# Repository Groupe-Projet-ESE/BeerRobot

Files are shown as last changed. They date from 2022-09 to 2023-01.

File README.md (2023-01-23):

# <div align="center">BeerRobot</div> 
__Last update of README__ : 23/01/2023

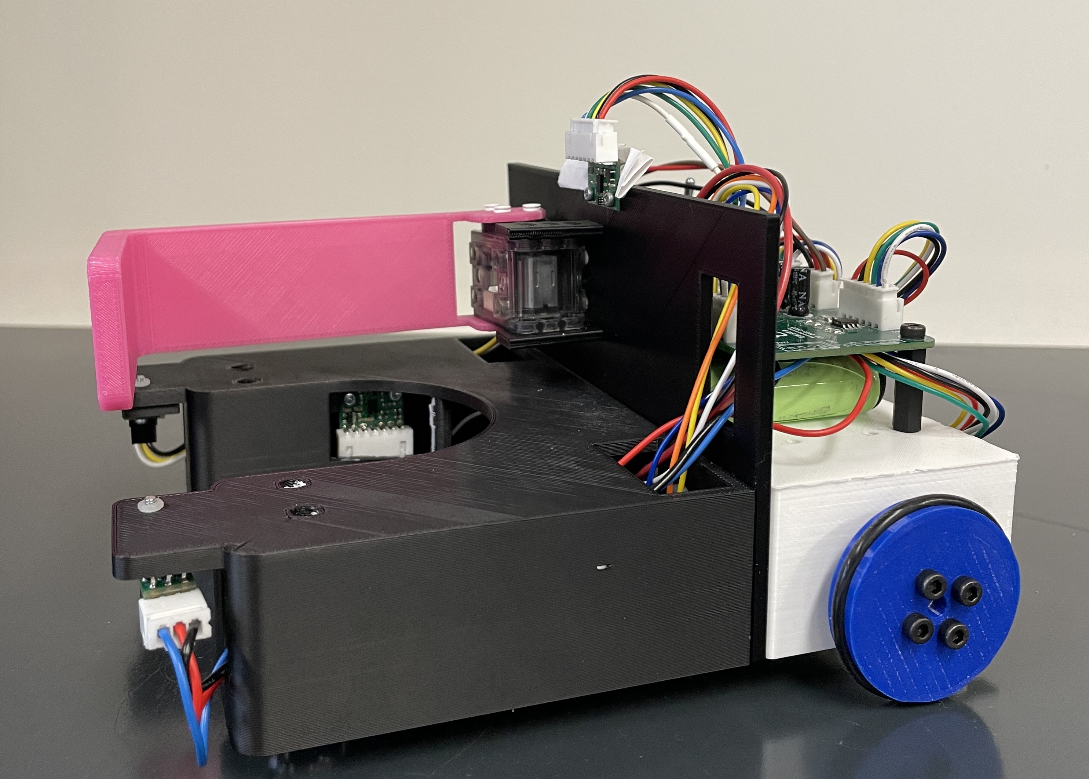
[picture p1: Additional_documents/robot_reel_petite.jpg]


## Introduction
Elèves en option ESE (Electronique et Systèmes Embarqués) au sein de l'ENSEA (Ecole Nationale Supérieures de l'Electronique et de ses Applications), réalisant un robot comme projet central de leur option.  

## Objectifs du projet
Le but du projet est de créer un robot permettant d'attraper des canettes, de relever la couleur de cette dernière, se déplacer avec la canette attrapée et la déposer dans la zone adaptée selon sa couleur. Par ailleurs le robot devra se repérer sur une table afin de ne pas tomber.   

## Matériels et composants à notre disposition

__Microcontroleur__ : STM32G070RBT6 (Farnell : 3365377)  
__Quartz 16 MHz__ : (Farnell : 2853935)  
__Connecteur SWD/STLink__ : (Farnell : 3226055)  
__Driver moteur__ : ZXBM5210-S (Farnell : 3935372)   
__Moteurs__ : DfRobot FIT0520 ou FIT0521   
__Régulateur 5V__ : AZ1117CH2-5.0TRG1 (Farnell : 3942512)  
__Régulateur 3.3V__ : MIC5317-3.3YM5 (Farnell : 2920683)  
__Batterie NIMH 7.2V 1.3Ah__ (RS : 777-0377)    
__Capteur bordure__ : Sharp GP2Y0D805Z0F (Generationrobots : A-000000-00046)   
__Capteur TOF__ : VL53L0X (Generationrobots : A-000000-03233)   
__Capteur de couleur__ : VEML3328 (Farnell : 3517203)  
__Servomoteur__ : XL320 (Generationrobots : A-000000-01282)  
Connecteurs JST 2.54mm  

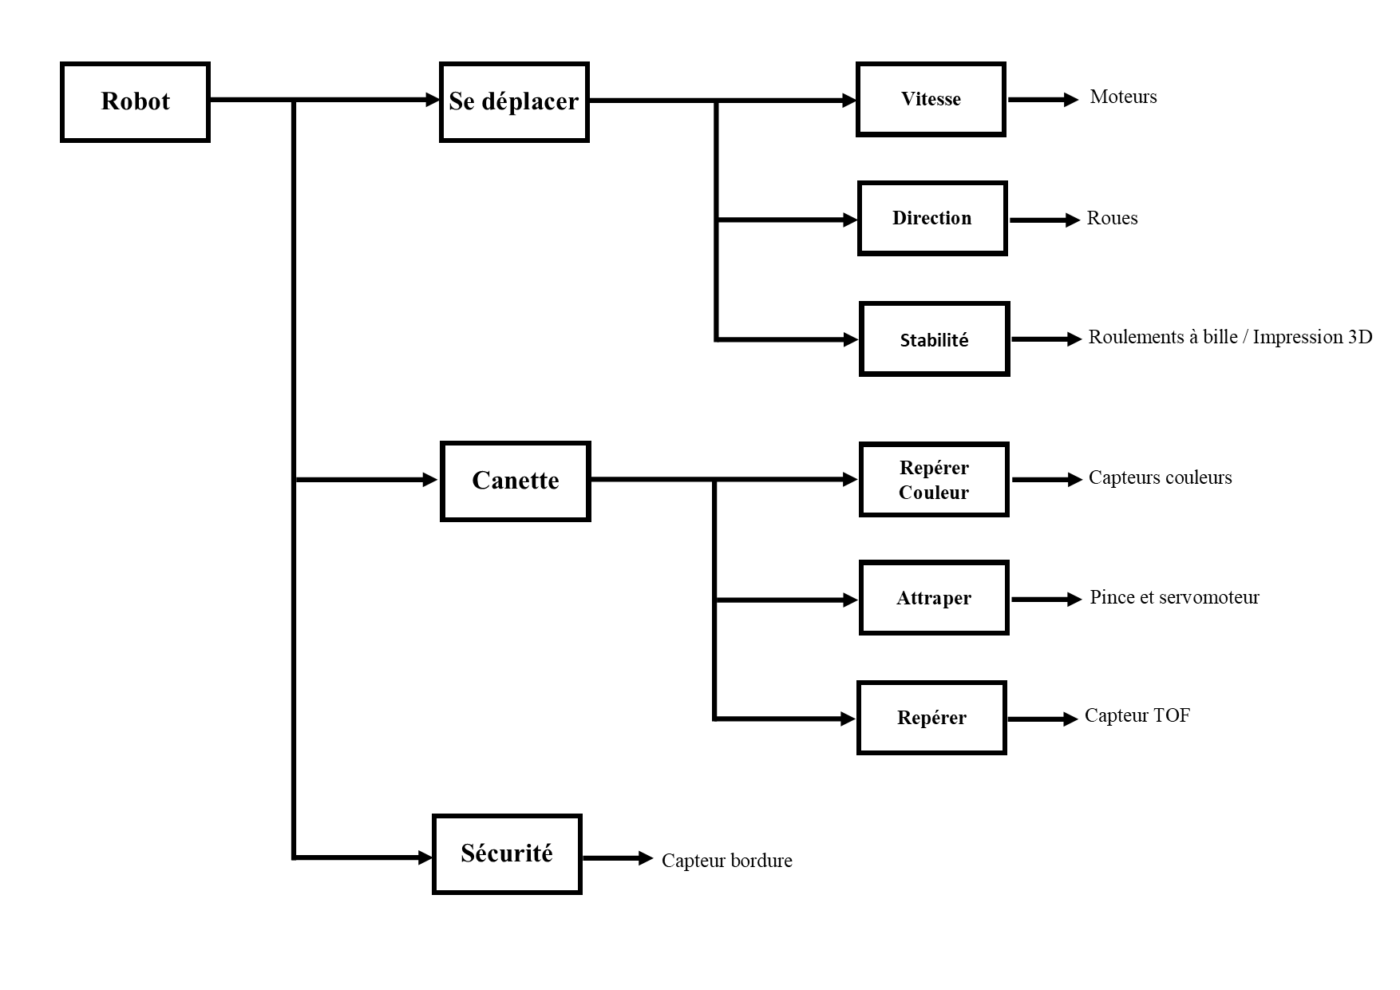
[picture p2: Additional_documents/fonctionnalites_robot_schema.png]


## Membres du groupe et rôles
Le groupe de projet est constitué de 4 membres, chacun ayant divers responsabilités.  
- __Chelsea COMLAN__ : responsable Hardware
- __Loïcia KOEHL__ : responsable intégration
- __Quentin SIMON__ : responsable Software
- __Alix HAVRET__ : responsable livrables

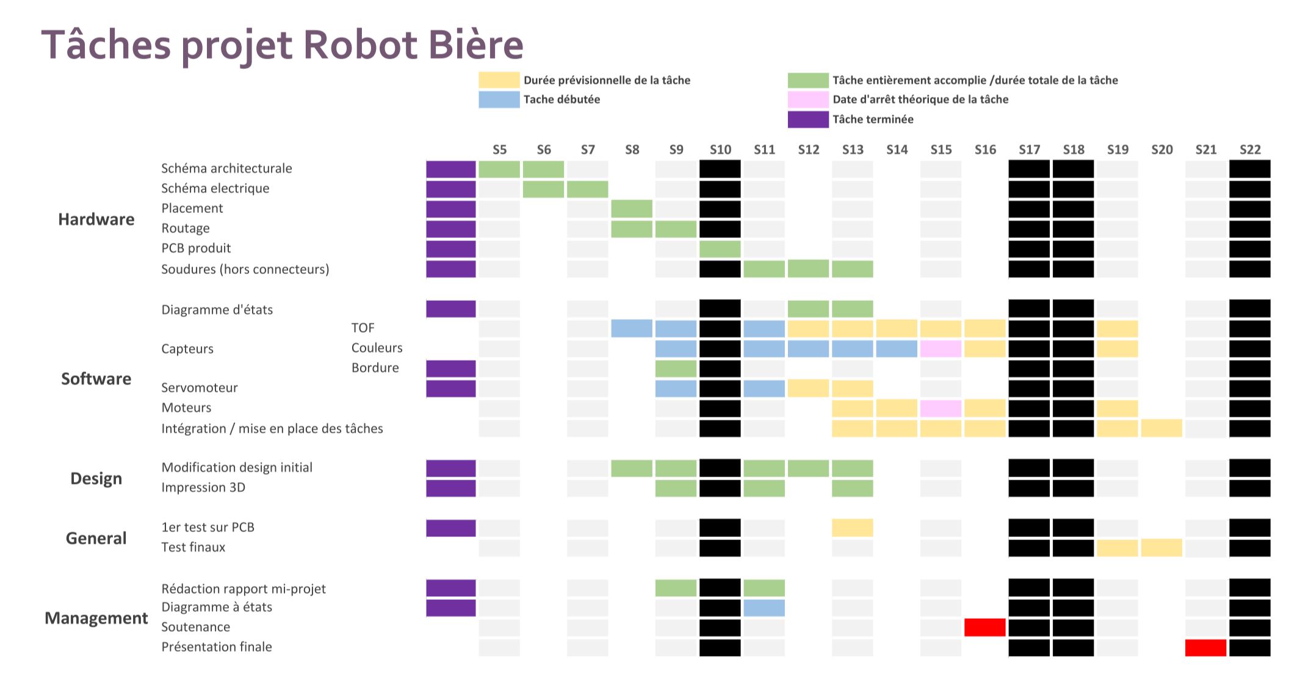
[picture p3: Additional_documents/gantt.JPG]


__Encadrants du projet__ : Mr Fiack , Mr Tauvel  
__Intervenants extérieur__ : Mme Quittel, Mr Jauffrey, Mr Le Bidan  

### Contenus des dossiers
La démonstration finale se trouve sur la master. 

#### Additional documents
Contient l'ensemble des images necessaire à la rédaction de ce README, le rapport de mi-projet rédigé en novembre ainsi que le diaporama de notre présentation du robot en décembre.   

  #### Hardware
Contient le projet Kicad avec l'ensemble des fichiers electronique ainsi que le fichier de routage du PCB.  
Le PCB a été produit à l'extérieur de l'ENSEA.  

  #### Software 
Contient les codes "annexes", c'est à dire les codes des composants testé sur le STM32F746NG.  
Le projet CubeIDE a destination de la STM32G0 (notre microcontroleur de projet) se trouve sur la master. 

  #### 3D 
  Contient certains fichiers 3D pour la réalisation du robot

## Architecture générale du projet

Au debut du projet nous avons eu la liste de l'ensemble des composants auxquels nous avions accès pour la réalisation du robot et afin de remplir ses divers fonctionnalités.   
Le schéma architectural au début du projet nous a permit de définir l'ensemble des entrées necessaires dans notre microcontroleur et les divers flux de données qui allaient entrer en jeu.  
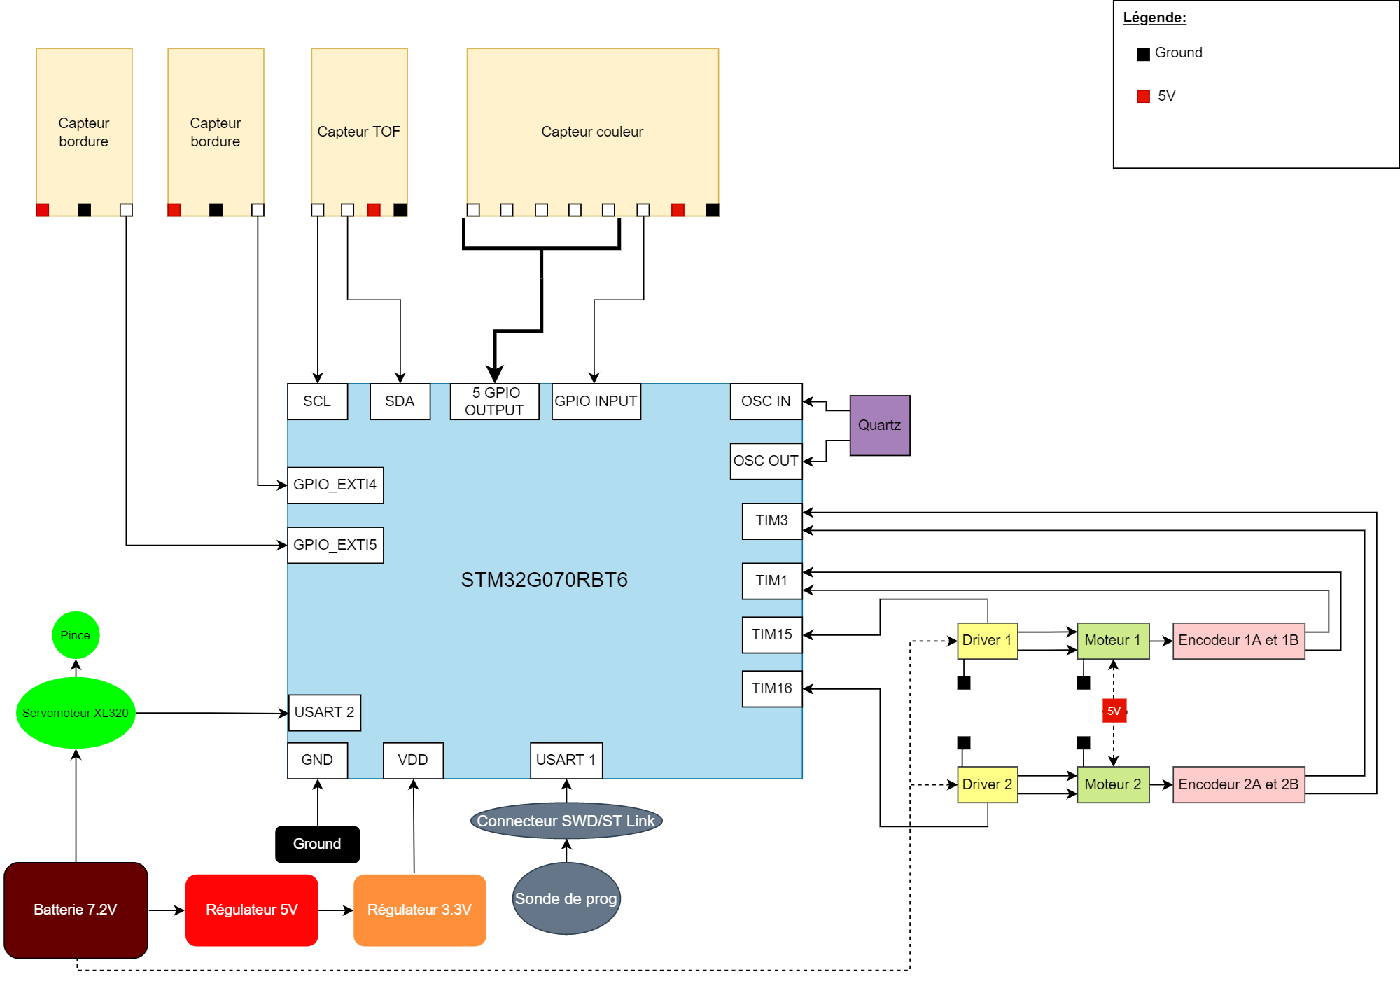
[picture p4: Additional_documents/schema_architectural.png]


### Rôles et utilité des divers composants, capteurs 
#### Moteurs FIT501
Deux Moteurs à courant continu, alimenté en xx V, permettant de faire tourner 2 roues. Le moteur a également un encodeur.  

### Servomoteur XL320
Servomoteur qui permettra de faire bouger la pince necessaire pour saisir les canettes.

### Capteur couleur TCS3200
Capteur permettant de detecter la couleur de la canette à l'aide de filtres superposés à des LEDS.

### Capteur de bordure 
Capteur infra-rouge qui détecte si il y a un object en face de lui.

### Capteur TOF 
Time Of Flight, renvoie le temps qu'a prit la source lumineuse du capteur pour rebondir sur un object et revenir. Cela nous permet d'avoir notre distance par rapport à un objet. (en mm)

## 3D du robot 
Nous avons prit la décision de modifier le design initial du robot sur onshape.  
Ajout d'un roulement en plus à l'avant, modification de l'emplacement de la pince et la forme de celle ci. Une fois le PCB reçu, des modifications ont été effectuées afin de permettre un bon placement de l'ensemble des fils.  
Par ailleurs nous avons aménagés divers emplacements pour les différents capteurs : couleurs, bordure et distance. 

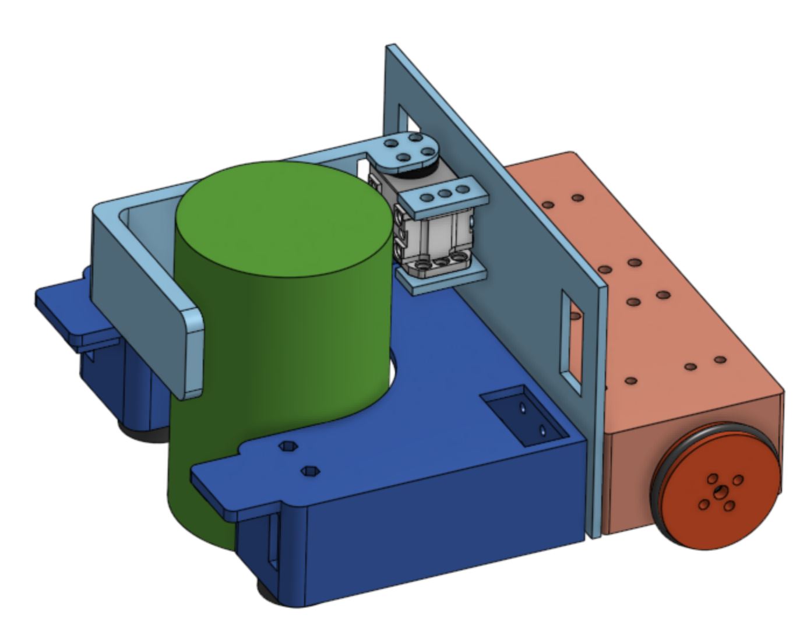
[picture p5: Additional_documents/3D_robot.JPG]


## Hardware 
### Schema electrique
A partir du schema architectural réalisé au début du projet, nous avons commencé le schéma électrique du projet sur Kicad.  
Ce dernier a été séparé en plusieurs feuilles afin de pouvoir organiser les différentes partie : STM32, alimentation, capteurs, moteurs, servomoteur.

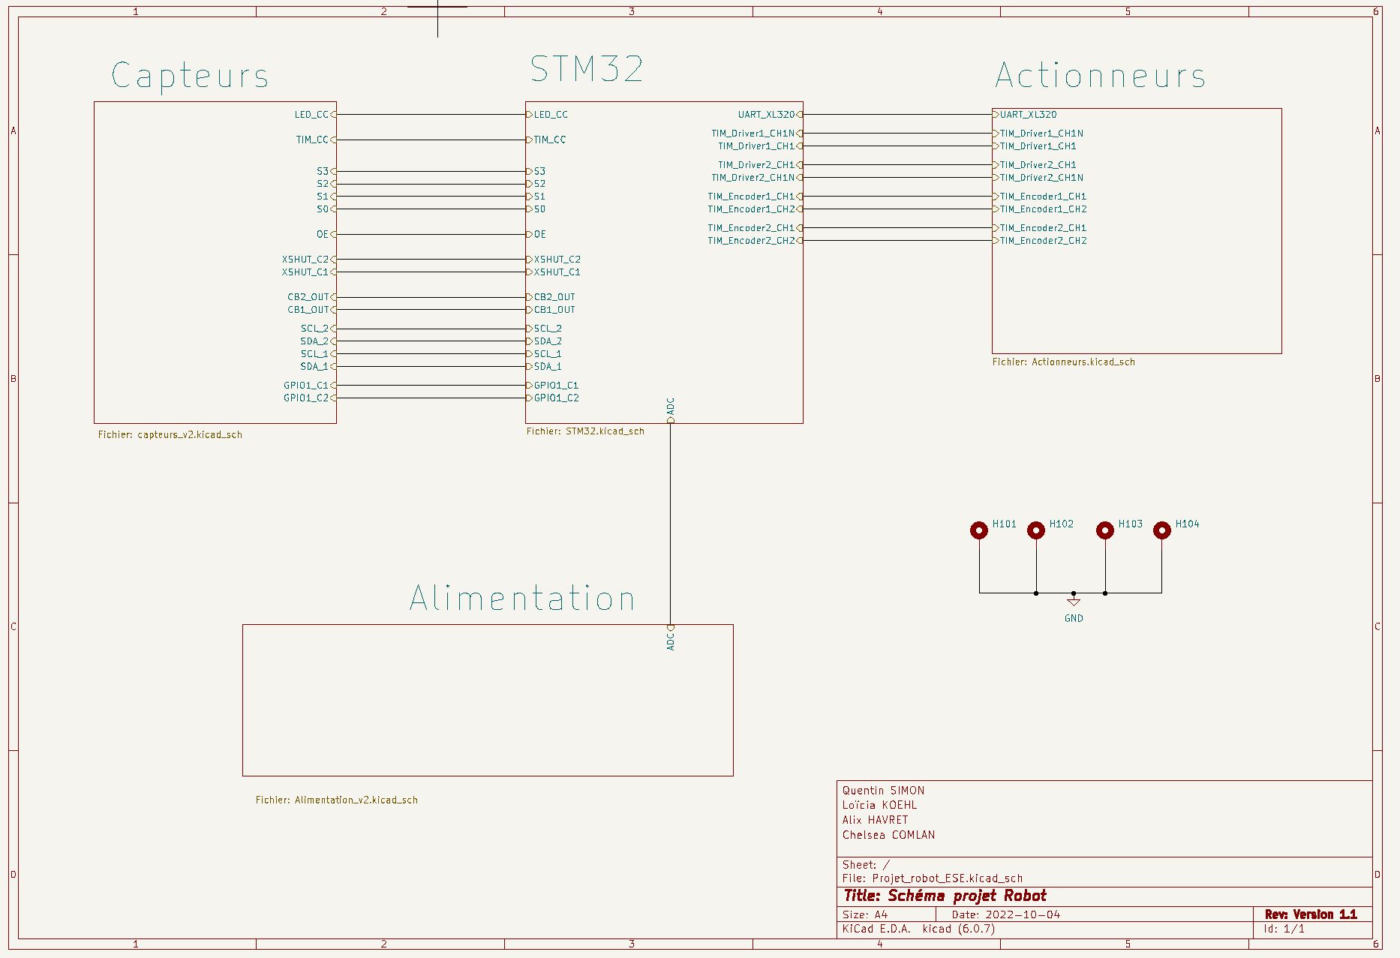
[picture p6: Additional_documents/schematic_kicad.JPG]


### PCB
__09/11/2022__ Reception du PCB  
__Soudeurs__ : Loïcia et Chelsea  
L'ensemble des soudures ont été réalisées à la main, lee 25/11/2022  l'ensemble des composants étaient soudés sur la carte.   
Nous avons soudés les connecteurs au fur et à mesure de la réalisation des tests.

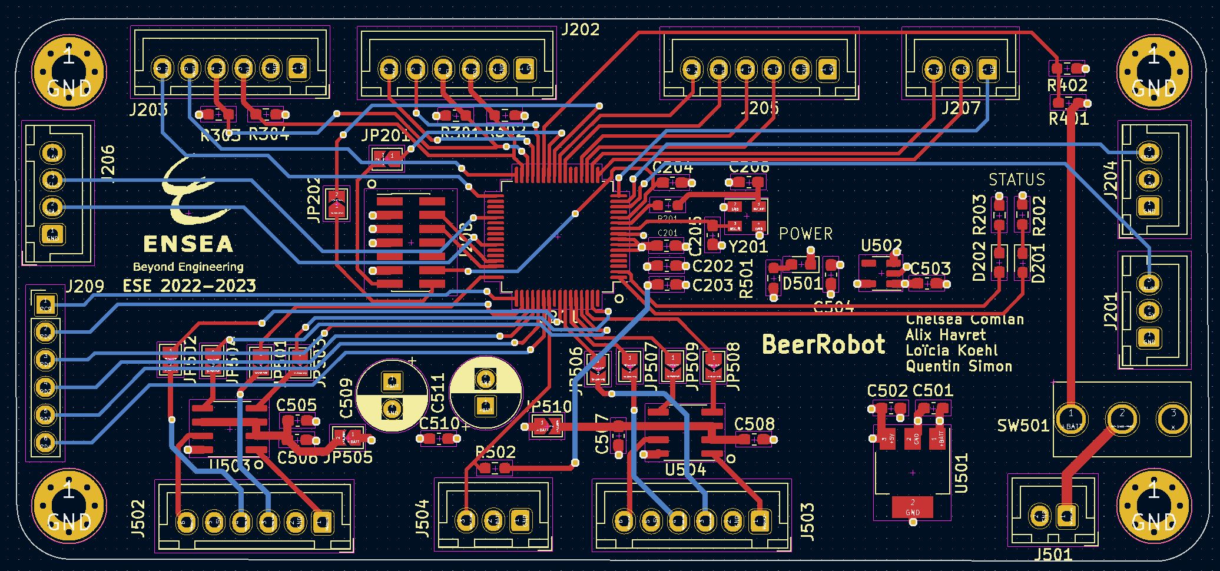
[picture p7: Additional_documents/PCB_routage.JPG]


## Software

Le code sera utilisé dans diverses tâches (utilisation de FreeRTOS). Chaque état décrit dans le diagramme à états correspondra à une tâche.  
Une tâche pourra faire appel à de la donnée, ou en consommer. Dans chaque tâche nous feront appel à divers bouts de code permettant de démarrer un capteur, un moteur, un servo, etc ...  

Pour effectuer nos tests sur les capteurs, nous avons implémentés un shell. Chacun des capteurs ont été validé sur la STM32F746NG, et ensuite leur code était intégré à la STM32G0.
La shell nous a permit de faire une première démonstration. 

### Moteurs : 
Après les premiers tests, nous avons remarqué que pour une même commande vitesse, les 2 roues ne tournaient pas à la même vitesse, de ce fait le robot n'allait pas droit.  Afin de régler ce problème il était nécessaire de mettre en place un asservissement.
#### Asservissement 
Nous avons décidé de faire un correcteur PI (Proportionnel Intégral).  

**schéma**

Pour cela il nous fallait donc récupérer des informations venant du robot et du microcontroleur :  
-	Valeur vitesse demandée  pour les roues
-	Valeur vitesse réelle des 2 roues (les 2 étant différentes du à la qualité des moteurs)  
-	Nombre de tick moteur  

Ces infos nous permettaient alors de créer le correcteur PI avec :  
-	Coefficient proportionnel Kp  
-	Coefficient intégrateur Ki  

Une fois avoir réussi à récupérer la valeur de la vitesse en entrée et le nombre de tick nous avons pu commencer à coder l’asservissement.  

Pour ce faire il fallait que l’on fasse la différence de valeur entre la valeur actuelle et la valeur précédente de vitesse. Par la suite, nous pouvions calculer l’erreur entre la valeur d’entrée et la vitesse du robot pour voir si il avançait à la vitesse souhaitée.  
Une fois toutes la valeurs et calculs mis en place, nous avons pu commencer la recherche des valeurs pour nos coefficients. Il fallait trouver les valeurs avec lesquelles il y avait le moins d’oscillation possible.  

### Fonctionnement des capteurs 
#### Capteur bordure 

#### Capteur TOF 
Le capteur TOF a un driver déja créé, ce qui nous a permit de réutiliser les fonctions déja existantes permettant l'initialisation du capteur, et la récupération des valeurs .L'activation de la pin GPIO nous permet d'acquérir les valeurs en continue tant que le TOF est actif.   
Lorsque que l'on veut utiliser 2 TOF, c'est la pin XSHUT qui rentre en jeux. Les 2 TOF étant sur le même I2C, on activera uniquement le TOF du capteur que l'on veut utiliser.  

#### Capteur couleurs
Non fonctionnel.

__Objectif de la présentation finale :__

La démo implémentée et téléchargée sur la master permet au robot de faire une première phase de démarrage, de se lancer en mode "recherche" canette. Une fois une canette repérée à une certaine distance, le robot continue sa recherche vers la zone où il a capté une canette. Une fois que la canette est captée dans le creue du robot, alors la pince est déclenchée en mode fermeture.

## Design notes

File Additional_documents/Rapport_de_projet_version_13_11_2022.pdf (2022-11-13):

# Rapport de projet de 3

# ème

# année option ESE

# Robot bière

### Encadrants

## - Mr FIACK Laurent - Mr TAUVEL Antoine

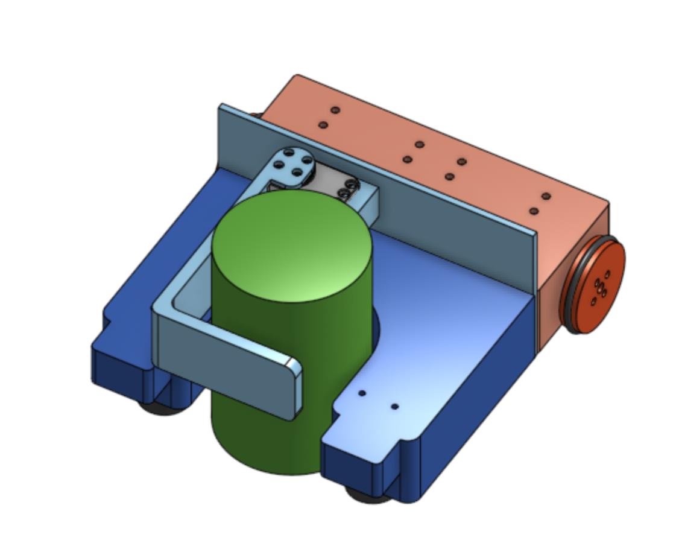
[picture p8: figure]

## COMLAN Chelsea - KOEHL Loïcia - HAVRET Alix - SIMON Quentin

## Novembre 2022

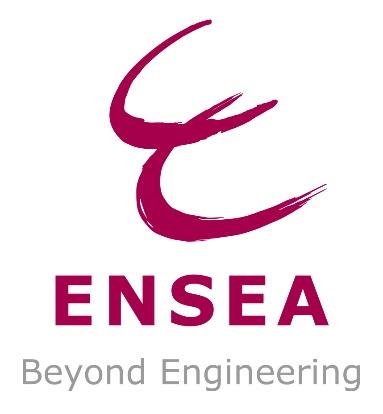
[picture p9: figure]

Rapport de projet | Version du 12/11/2022

1 Introduction_____________________________________________________________________________________3

1.1 Présentation et objectif du défi “Robot Bière"___________________________________________ 3 1.2 Analyse fonctionnelle /CDC_________________________________________________________________ 3 1.3 Organisation du projet ______________________________________________________________________ 4
1.3.1 | GitHub _______________________________________________________________________________________________4
1.3.2 | Equipe _______________________________________________________________________________________________4
1.3.3 | Planning _____________________________________________________________________________________________4
2 Architecture du projet ________________________________________________________________________5

2.1 Ressources ____________________________________________________________________________________ 5 2.1.1 Matérielles___________________________________________________________________________________________5 STM32G070RBT6 _____________________________________________________________________________________________5 2.1.2 Logicielles ___________________________________________________________________________________________5
3 Étapes du développement ____________________________________________________________________6

3.1 Hardware ______________________________________________________________________________________ 6 3.2 CAD _____________________________________________________________________________________________ 6 3.3 Software _______________________________________________________________________________________ 6
3.3.1 | Capteur de bordure _________________________________________________________________________________6
3.3.2 | Capteur couleur VEML3328________________________________________________________________________8
3.3.3 | Capteur couleur SEN0101__________________________________________________________________________9
3.3.4 | Capteur TOF VL53L0X____________________________________________________________________________ 10
3.3.5 | Servomoteur XL320 ______________________________________________________________________________ 11
4 Conclusion _____________________________________________________________________________________14 ANNEXES____________________________________________________________________________________________15

Annexe 1 : schéma architectural _________________________________________________________________15 Annexe 2 : pinout view_____________________________________________________________________________16 Annexe 3 : Schématique capteur couleur 3.3V_________________________________________________16 Annexe 4 : Liste des figures _______________________________________________________________________17

### 1 Introduction

### 1.1 Présentation et objectif du défi “Robot Bière"

Élèves en option ESE (Electronique et Systèmes Embarqués) au sein de l'ENSEA (Ecole Nationale Supérieure de l'Electronique et de ses Applications), réalisant un robot comme projet central de leur option.

Création d'un robot permettant d'attraper des canettes et les déplacer dans des zones, délimitées aux préalables, selon la couleur de la canette.

Le robot devra être capable de :
- Se déplacer
- Saisir une canette
- Se déplacer avec la canette
- Détecter la couleur de la canette
- Ne pas tomber
- Déplacer la canette dans la zone correspondante

### 1.2 Analyse fonctionnelle /CDC

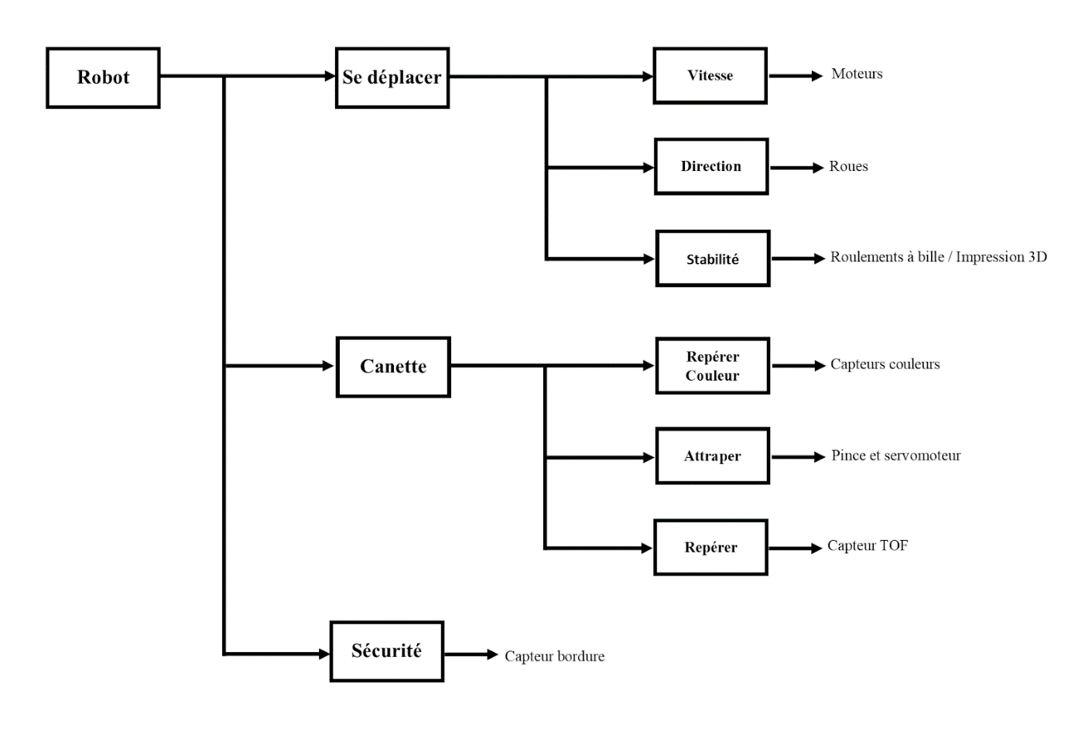
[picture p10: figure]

Figure 1 Analyse fonctionnelle

### 1.3 Organisation du projet

### 1.3.1 GitHub

Github projet (https://github.com/Groupe-Projet-ESE/BeerRobot)

### 1.3.2 Equipe

- Chelsea COMLAN : responsable hardware
- Loïcia KOEHL : responsable intégration
- Quentin SIMON : responsable software
- Alix HAVRET : responsable livrable

### 1.3.3 Planning

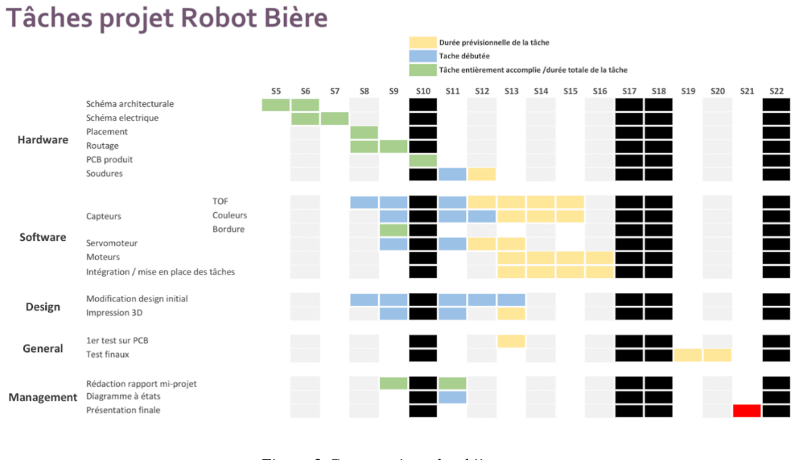
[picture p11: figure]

Figure 2 Gantt projet robot bière

### 2 Architecture du projet

### 2.1 Ressources

### 2.1.1 Matérielles

Nom du composant | Référence
STM32G070RBT6 | Farnell : 3365377
Quartz 16 MHz | Farnell : 2853935
Connecteur SWD/ST Link | Farnell : 3226055
Driver moteur : ZXBM5210-S | Farnell : 3935372
Moteurs FIT 0520 | DfRobot FIT0520
Régulateur 5V AZ1117CH2-5.0TRG1 | Farnell : 3942512
Régulateur 3.3V MIC5317-3.3YM5 | Farnell : 2920683
Batterie NIMH 7.2V 1.3Ah | RS : 777-0377
Capteur bordure | Sharp GP2Y0D805Z0F
Capteur TOF | VL53L0X
Capteur de couleur 5V | SEN0101
Capteur de couleur 3.3V | VEML3328
Servomoteur : XL320 | Generationrobots : A-000000-01282

Connecteurs JST 2.54mm

LED + R/C

Pour notre projet, nous aurons également besoin du matériel de laboratoire : oscilloscope, générateur, multimètre, station de soudures

### 2.1.2 Logicielles

Partie Software
- Cube IDE

PCB
- Kicad pour la réalisation
- JCLPCB pour la production

Design du robot
- On Shape pour la réalisation
- ENSEA pour la production

### 3 Étapes du développement

### 3.1 Hardware

Pour structurer notre carte électronique nous avons dans un premier temps réalisé un schéma architectural (cf Annexe 1)

Ce schéma recense l’ensemble des composants nécessaires au bon fonctionnement de notre robot, ainsi que l’ensemble des ports sollicités.
La visualisation de l’ensemble des ports nécessaires a été faite sur CubeIDE avec le microcontrôleur correspondant (cf Annexe 2).

Sur Kicad nous avons traduit le schéma architectural, avec l’ensemble des composants, et broches nécessaires. Par la suite, le placement et le routage a été réalisé pour être contenu sur un PCB 4 couches de dimensions 11 par 4.

Une fois les PCB reçus, la soudure a débuté.

### 3.2 CAD

En parallèle de la conception du PCB, intéressons-nous à la forme que prendra notre robot. Nous partons du design proposé sur OnShape auquel nous ajoutons ou modifions certaines parties.

Pour assurer la stabilité du robot nous voulons qu’il compte deux roues folles à l’avant, de part et d’autre du creux pouvant accueillir la canette. Pour ce faire, nous devons déplacer le servomoteur qui commande le clapet de la pince afin de placer de manière symétrique les deux roues folles. La pince prend une forme différente, fixée au fond du creux qui accueille la canette.

Afin de placer et fixer les différents capteurs sur le robot, nous créons des ouvertures ainsi que des parois de fixation liées aux dimensions des différents composants comme pour les capteurs TOF qui seront placés à l’avant du robot, le capteur couleur au fond du creux pour la canette et le servomoteur juste au-dessus.

Une fois toutes les pièces modifiées, nous envoyons le design pour impression 3D et attendons que les pièces de notre robot soient fabriquées pour pouvoir l’assembler puis le tester voire l’améliorer.

### 3.3 Software

### 3.3.1 Capteur de bordure

Pour détecter les bordures de la table, on utilise un capteur de bordure Sharp. Ce dernier sera positionné en amont du robot et des roulements à bille, en pointant vers la table.

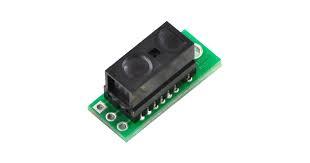
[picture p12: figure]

Figure 3 Capteur de bordure

Il envoie un rayon laser pour détecter si un objet se trouve à une distance inférieure à 5 cm. Si c’est le cas, la sortie est à l’état bas. Sinon, la sortie est à l’état haut.

Le capteur est alimenté avec le régulateur 5V.
Son fonctionnement a été testé avec la carte STM32F746NG.

Ainsi, pour empêcher une chute, on branche la sortie du capteur sur un GPIO en mode EXTI. Puis on active une interruption à chaque front montant.

Putty nous permet d’observer le bon fonctionnement du code.

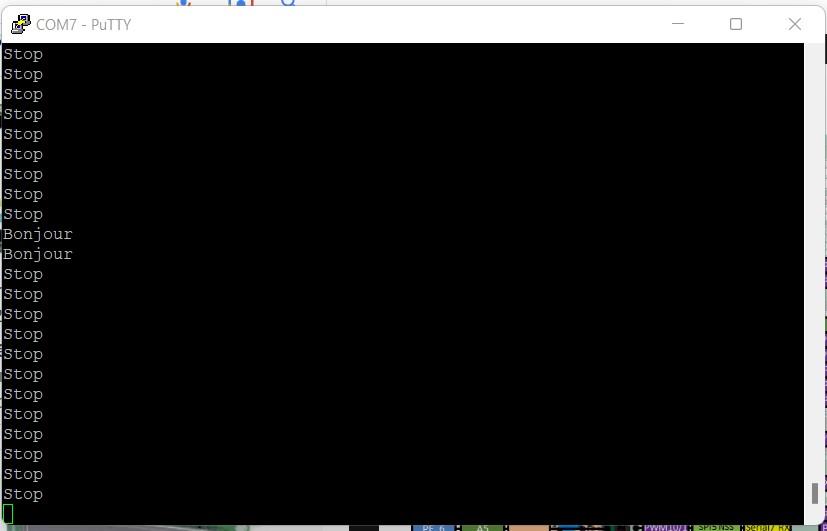
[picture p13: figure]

Figure 4 Sortie de la console TeraTerm pour l'utilisation du capteur de bordure

A terme, le capteur sera placé en amont du robot. Si le vide est détecté, le message d’erreur sera remplacé par une commande d’arrêt moteur, suivi d’une commande de rotation.

On remarque qu’on obtient bien le changement d’état en parallèle à l’oscilloscope.

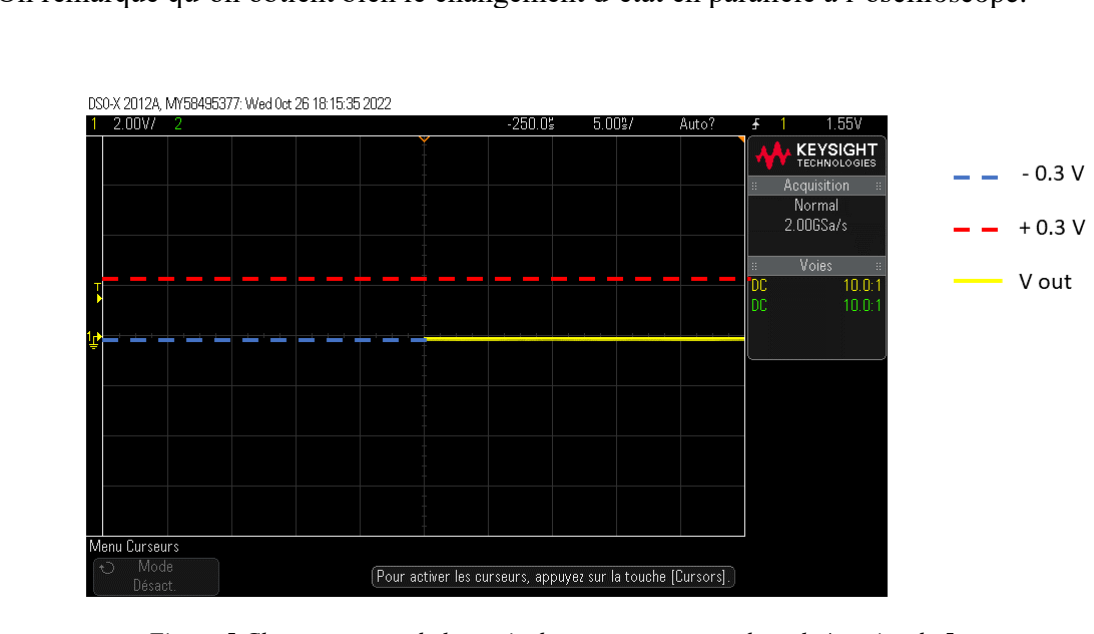
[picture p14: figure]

Figure 5 Chronogramme de la sortie du capteur avec un obstacle à moins de 5 cm

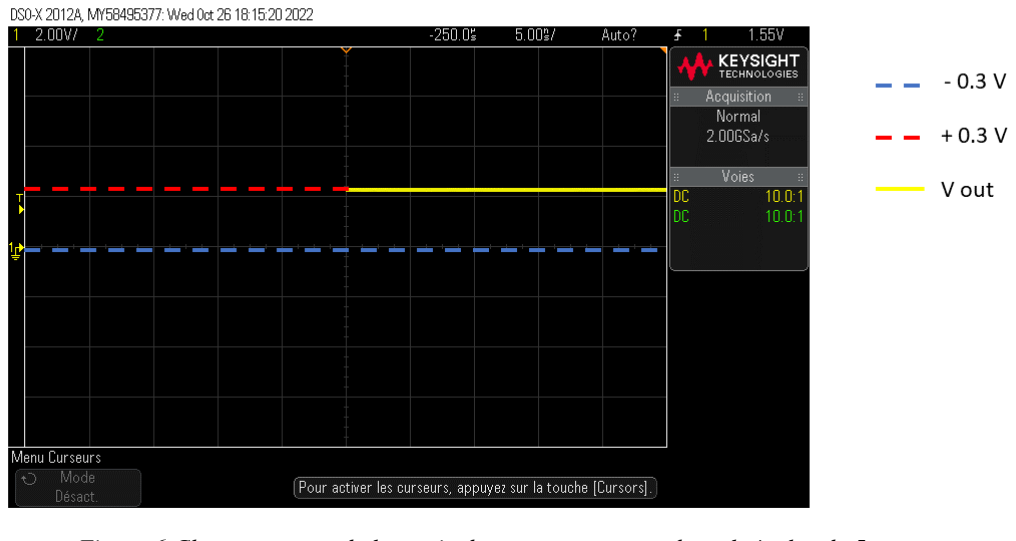
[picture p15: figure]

Figure 6 Chronogramme de la sortie du capteur avec un obstacle à plus de 5cm

### 3.3.2 Capteur couleur VEML3328

Pour détecter la couleur des canettes nous allons utiliser le capteur de couleur VEML3328.

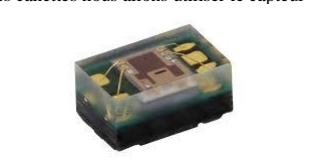
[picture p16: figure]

Figure 7 Capteur couleur VEML3328

Ce capteur mesure la valeur de bleu, rouge, vert et IR d’un objet. Il stocke les valeurs dans des registres sur 16 bits. Le microcontrôleur peut accéder à ces valeurs par liaison I2C, grâce à l’adresse du capteur 0x10 et les codes de commande, 0x05 pour le rouge et 0x06 pour le vert.

Avant toute chose, il faut configurer le capteur grâce au code de commande 0x00.

Cependant, il fonctionne avec une tension d’entrée de 3.3V contrairement à l’autre composant de la carte. C’est pourquoi nous avons réalisé un autre PCB pour le capteur.

Compositions du PCB :

- 4 diodes et 4 résistances pour éclairer la canette
- Un régulateur 3.3V pour alimenter le capteur
- 2 résistances de pull-up pour la communication I2C
- 3 condensateurs de découplage pour le régulateur et le capteur

Cf Annexe 3.

### 3.3.3 Capteur couleur SEN0101

Nous utiliserons un second capteur de couleur. Le SEN0101 de chez DFRobot comprend une puce capteur couleur et 4 LEDs blanches.

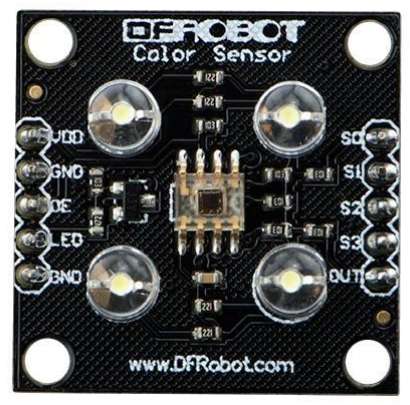
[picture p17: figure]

Figure 8 Capteur couleur SEN0101

Il peut être alimenté en 3.3V ou 5V, on l'alimente par le régulateur 5V. L’utilisation du capteur est testée avec une carte STM32F746NG.

Dans un premier temps, les 4 LEDs blanches sont allumées en mettant à 1 le signal envoyé sur la pin LED du capteur. Le capteur est bien alimenté.

Pour faire fonctionner le capteur, les pins S0, S1, S2, S3 ainsi que le port LED sont branchés sur des ports GPIO_Output. La liaison UART qui passe par le port USB de la carte est elle aussi configurée pour avoir des retours pendant que le code tourne sur la carte afin de débugger. Le but est, à terme, d’afficher la couleur détectée.

Les pins S2 et S3 permettent de choisir le filtre pour détecter une couleur en particulier entre rouge, vert, bleu. Il est également possible de configurer le capteur sans filtre. Les pins 20 et S1 permettent de choisir l’échelle d'intensité lumineuse qui est reliée à la fréquence en sortie du capteur. Dans un premier temps, l’échelle de sortie en fréquence est à 100%.

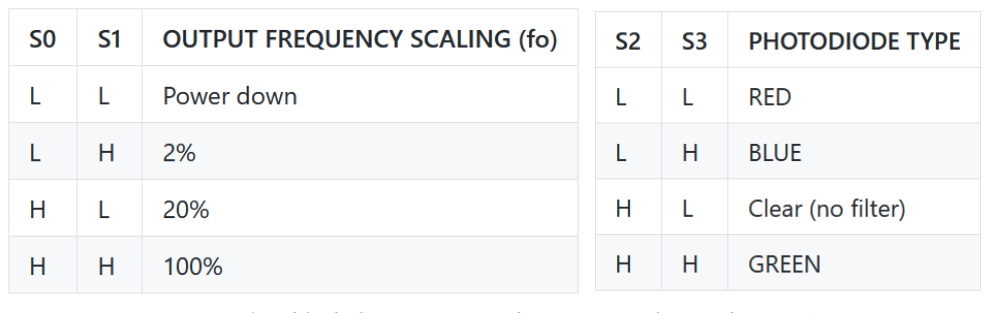
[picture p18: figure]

Figure 9 Table de fonctionnement du capteur couleur et des LEDS

La sortie Out récupère une fréquence qui permet de déterminer la couleur de la canette. La pin Out du capteur est reliée à un timer en mode Input Capture afin de mesurer la fréquence du signal qui sera capté par les photodiodes. Le capteur envoie un signal carré au STM et pour déterminer la fréquence du signal il faut faire la différence entre les temps des fronts montants sur une ou plusieurs périodes.

Mode de fonctionnement des mesures :

Pour lancer la première mesure avec le mode input capture, on utilise HAL_TIM_IC_Start_IT. Selon la configuration choisie, les différentes mesures sont effectuées sur les fronts montants ou descendants ou les deux et les valeurs sont stockées dans le registre IRQ_CCR. Plusieurs mesures permettent de faire une moyenne qui donnera un résultat plus fin de la fréquence et donc de la couleur de la canette. Après avoir effectué
plusieurs | mesures, | il | faut | stopper | les | interruptions | IC | avec | la | fonction
HAL_TIM_IC_Stop_IT.

A chaque interruption, le code appelé est dans la fonction HAL_TIM_IC_CaptureCallback. Le capteur est configuré pour recueillir deux temps de montée consécutifs et en faire la différence pour obtenir la période puis en déduire la fréquence grâce à l’horloge du timer.

A chaque interruption, un compteur est incrémenté pour faire un certain nombre de mesures qui seront moyennées et aussi pour changer le type de filtre. Pour debugger, des printf ont été utilisés dans le code d’interruption ce qui n’est pas recommandé et peut être amélioré. Pour l’heure, des fréquences sont affichées en sortie mais ne semblent pas cohérentes et il reste à moyenner les fréquences et à les faire correspondre aux couleurs pour vérifier la capacité du capteur à différencier et classer les canettes qui seront vertes et rouges.

### 3.3.4 Capteur TOF VL53L0X

Afin de pouvoir repérer les canettes, et la distance du robot vis à vis de ces dernières, nous utilisons un capteur TOF (Time Of Flight). Ce dernier relève la distance en cm (il nous offre une plage de mesure de distance jusqu'à 2 mètres) du capteur par rapport à un objet, quelle que soit sa couleur.

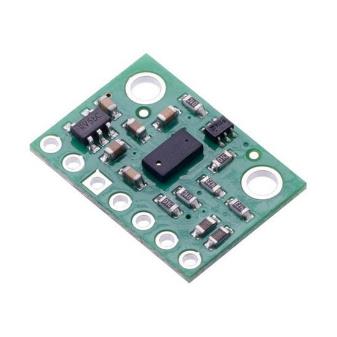
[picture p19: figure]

Figure 10 Capteur TOF VL53L0X

C’est la mesure du temps que met la lumière à revenir au capteur qui permet de déterminer sa distance aux objets

Le VL53L0X de chez STMicroelectronics est incorporé à un module pour rendre son utilisation plus facile d’accès. On utilise la STM32F746NG Discovery pour tester le module.

Le capteur TOF nécessite L’I2C (Inter Integrated Circuit). Le bus I2C permet de faire communiquer entre eux des composants électroniques très divers grâce à trois fils.

- Un signal de donnée : SDA
- Un signal d’horloge : SCL
- Un signal de référence électrique : Masse

Nous alimentons le capteur en 3.3V, et le capteur possède également une broche XSHUT (une entrée) et la broche GPIO1 (une sortie à drain ouvert).

Le VL53L0X possède une librairie (un driver) complète, nécessaire pour pouvoir utiliser les fonctions associées (démarrage, lecture, …).
Le driver une fois téléchargé dans le projet, les fonctions sont simples à utiliser. L’I2C permet d’obtenir des valeurs rapidement, la conversion de ces dernières se fera via des fonctions de la librairie.

Une structure principale contient l’ensemble des éléments nécessaires à la liaison avec l’I2C.

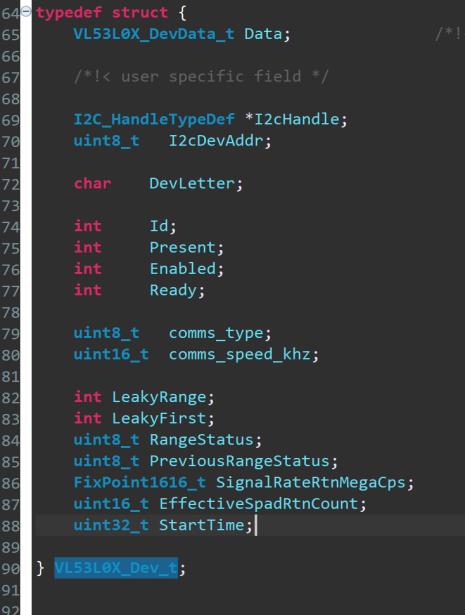
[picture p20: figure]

Figure 11 Structure de la librairie du VL54L0X

Dans notre projet l’objectif est de pouvoir donner la distance entre le robot et une canette, de ce fait une fois que la distance sera égale, ou proche de zéro, les moteurs devront s’arrêter pour que le robot s’arrête et que la pince prenne le relais.

### 3.3.5 Servomoteur XL320

Le servomoteur va nous permettre d’attraper la canette. Dès que le robot va détecter une canette il va avancer vers celle-ci et dès que la distance est bonne, le servomoteur va entrer en action en ouvrant la pince pour que le robot puisse saisir la canette. Nous avons donc commencé par essayer de comprendre comment celui-ci pouvait fonctionner et comment on pouvait le faire tourner.

Figure 12 Servomoteur XL320

Mode de fonctionnement :

Le servomoteur nécessite l’envoie d’une trame. Différents modes sont disponibles, on teste dans un premier temps le mode « write » avec la gestion des LEDS et le mouvement du servomoteur.

Figure 13 Trame write à envoyer au servomoteur

Nous pouvons voir que les données Header, reserved sont fixés, nous n’avons pas à les modifier. Les bits CRC quant à eux sont calculés automatiquement dans le programme. Nous voulons l’utiliser en broadcast donc le packet id est fixé à la valeur donnée dans sa datasheet qui est de 0xFE. L’instruction correspond à ce que nous souhaitons faire. Pour écrire, on utilise la valeur 0x03.

Test LED :

Pour pouvoir allumer la led il faut écrire à l’adresse 0x19 qui correspond à la valeur 25 en décimal.

Figure 14 Commande de la LED

Nous avons testé de contrôler la LED que l’on peut mettre de différentes couleurs :

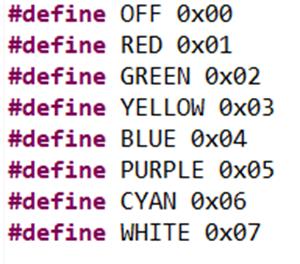
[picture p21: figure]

Figure 15 Commandes couleurs de la LED du servomoteur

Test

On allume la LED et ensuite on l’éteint, donc il nous faut la valeur 0 pour éteindre et 2 pour avoir la LED en vert.

Après l’envoi du code, voici les trames obtenues :

Figure 16 Trame reçue pour le fonctionnement de la LED

Les valeurs obtenues sont celles souhaitées.

Ensuite, nous sommes passé à tester la rotation du servo, pour cela la trame change car l’adresse change, maintenant nous avons l’adresse 0x1E pour le mode Goal Position :

Figure 17 Commande de la rotation du servomoteur

Nous entrons les paramètres souhaités avec la valeur que nous voulons, dans la datasheet nous avons trouvé que le servo-moteur pouvait aller de la position 0 à 1023 et en hexadécimal il faut écrire 0x00 pour la valeur 0 et 0x3FF.

Voici les trames obtenues :

Figure 18 Trame reçue pour la rotation du servomoteur

Si on regarde, nous pouvons voir que les premières données n’ont pas changé, nous changeons les données à partir de la valeur 7 car nous avons 7 valeurs par la suite avec l’instruction qui vaut 3 car on écrit, la valeur 1E correspond au mode que l’on veut donc pour nous la position, le ff 3 correspond à la position que l’on veut.

Dans notre cas nous testons pour la position 1023, juste qu’il faut faire attention car la première valeur correspond au bit de poids faible et les deux dernières valeurs sont calculées par la formule du code qui correspond au bit CRC.

La prochaine étape sera de gérer la vitesse du servomoteur et relier son fonctionnement, et donc l’ouverture de la pince lorsque l’on s’approchera d’une canette.

### 4 Conclusion

En 2 mois nous avons réalisé 90% de la partie hardware. Le PCB est produit, il ne manque que la soudure des composants.
Nous pourrons entamer les premiers tests sur la carte une fois que cette dernière sera prête avec l’ensemble des soudures réalisées.

Tous les capteurs ont un code qui est écrit/en cours d’écriture et testé sur la STM32F746NG Discovery. Les différents capteurs, le servomoteur et les moteurs devront agir ensemble, il nous faudra déterminer les différentes tâches à mettre en place (utilisation de FreeRTOS). Le diagramme d’états, une fois complet, nous permettra de définir les tâches à mettre en place.

Le design du robot a été repensé afin de pouvoir contenir l’ensemble des capteurs, une fois imprimé en 3D, une analyse sera effectuée quant aux emplacements des capteurs et le mode de fonctionnement de la pince, et une phase d’amélioration sera entamée pour obtenir un robot fonctionnel et où tous les capteurs auront un emplacement adapté (selon leur utilisation)

### ANNEXES

Annexe 1 : schéma architectural

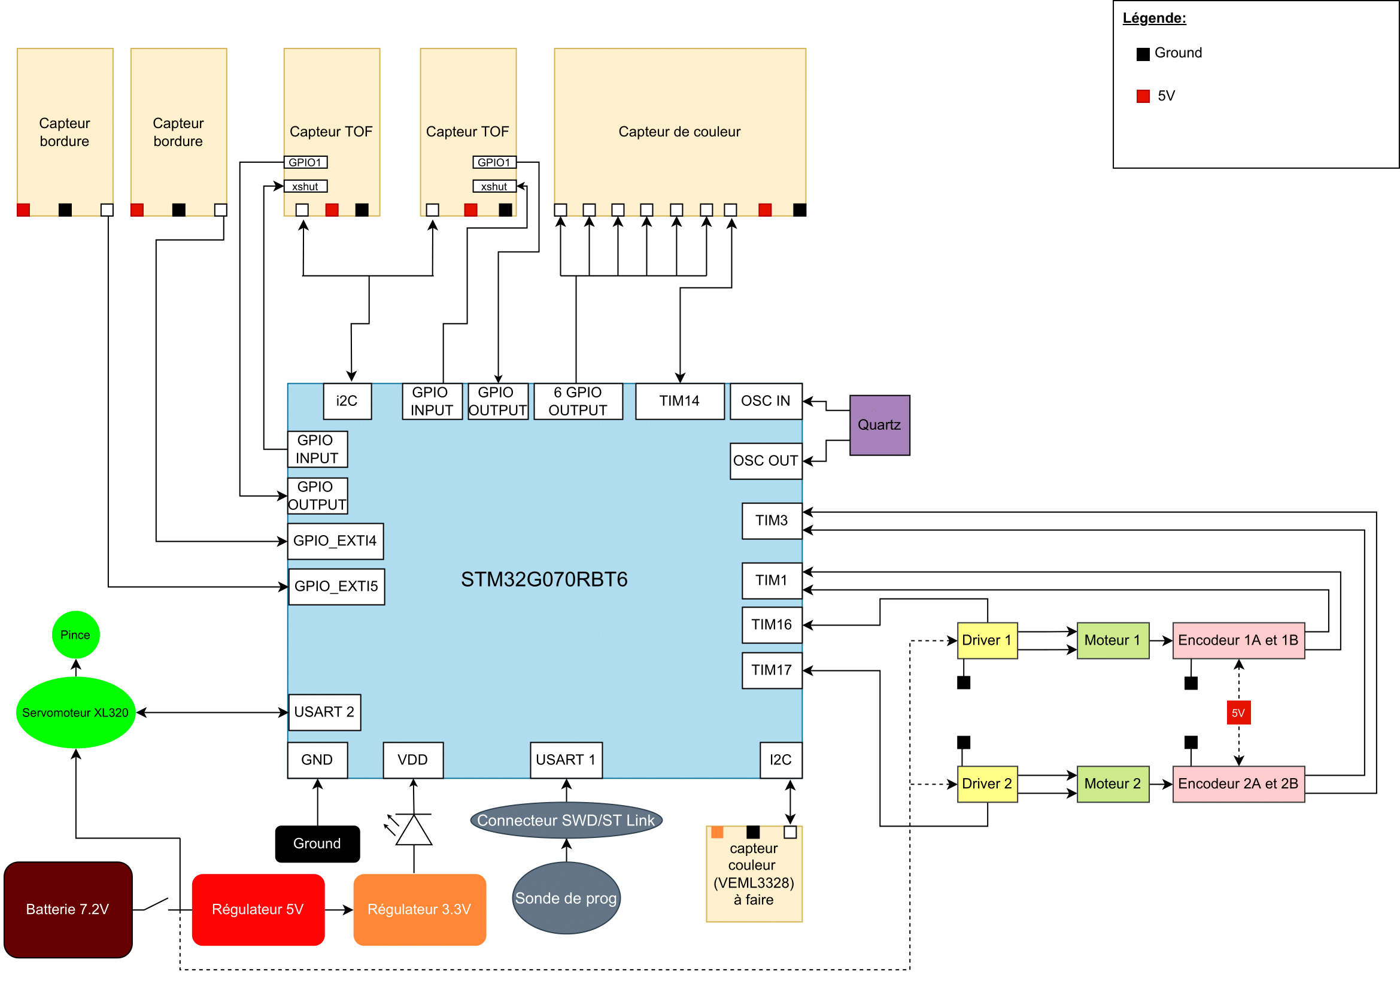
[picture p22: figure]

Figure 19 Schéma architectural

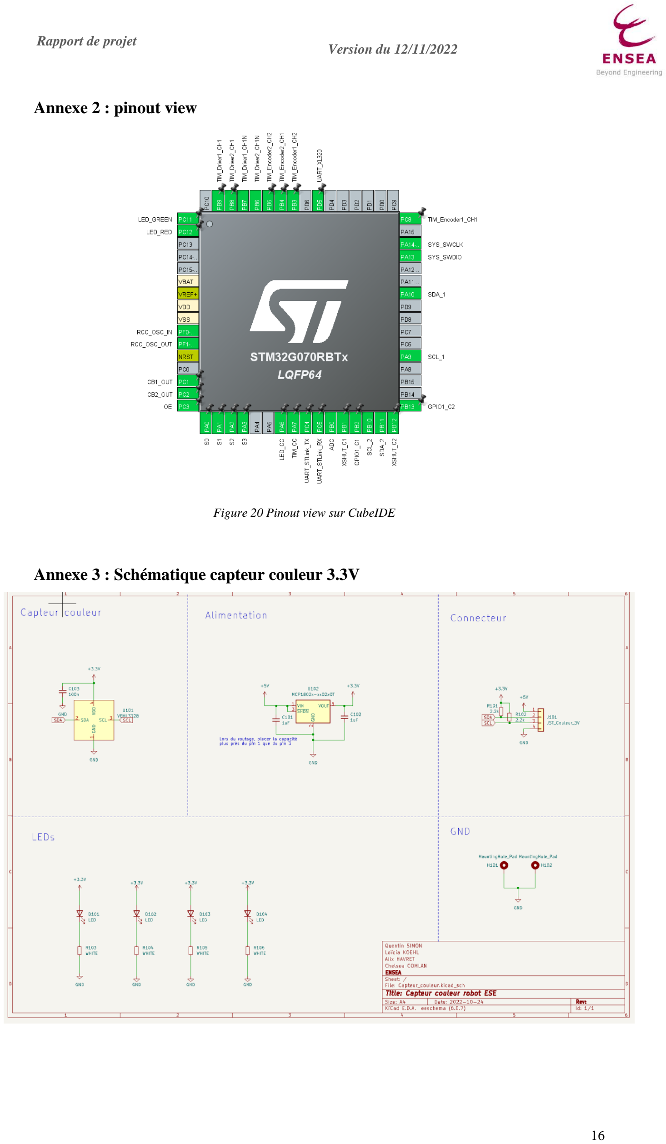
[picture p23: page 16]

Annexe 2 : pinout view

Figure 20 Pinout view sur CubeIDE

Annexe 3 : Schématique capteur couleur 3.3V

Annexe 4 : Liste des figures

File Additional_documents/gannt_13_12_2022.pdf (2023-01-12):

# Tâches projet Robot Bière

S5 | S6 | S7 | S8 | S9 | S10 | S11 | S12 | S13 | S14 | S15 | S16 | S17 | S18 | S19 | S20 | S21 | S22
Schéma architecturale
Schéma electrique
Placement
Routage
PCB produit

Diagramme d'états
TOF
Couleurs
Bordure
Servomoteur
Moteurs

Modification design initial Impression 3D

1er test sur PCB
Test finaux

Rédaction rapport mi-projet Diagramme à états
Soutenance
Présentation finale

Tâche entièrement accomplie /durée totale de la tâche Date d'arrêt théorique de la tâche
Tâche terminée

### Design

### General

### Management

### Hardware

### Software

Capteurs

Intégration / mise en place des tâches

Soudures (hors connecteurs)

Durée prévisionnelle de la tâche Tache débutée

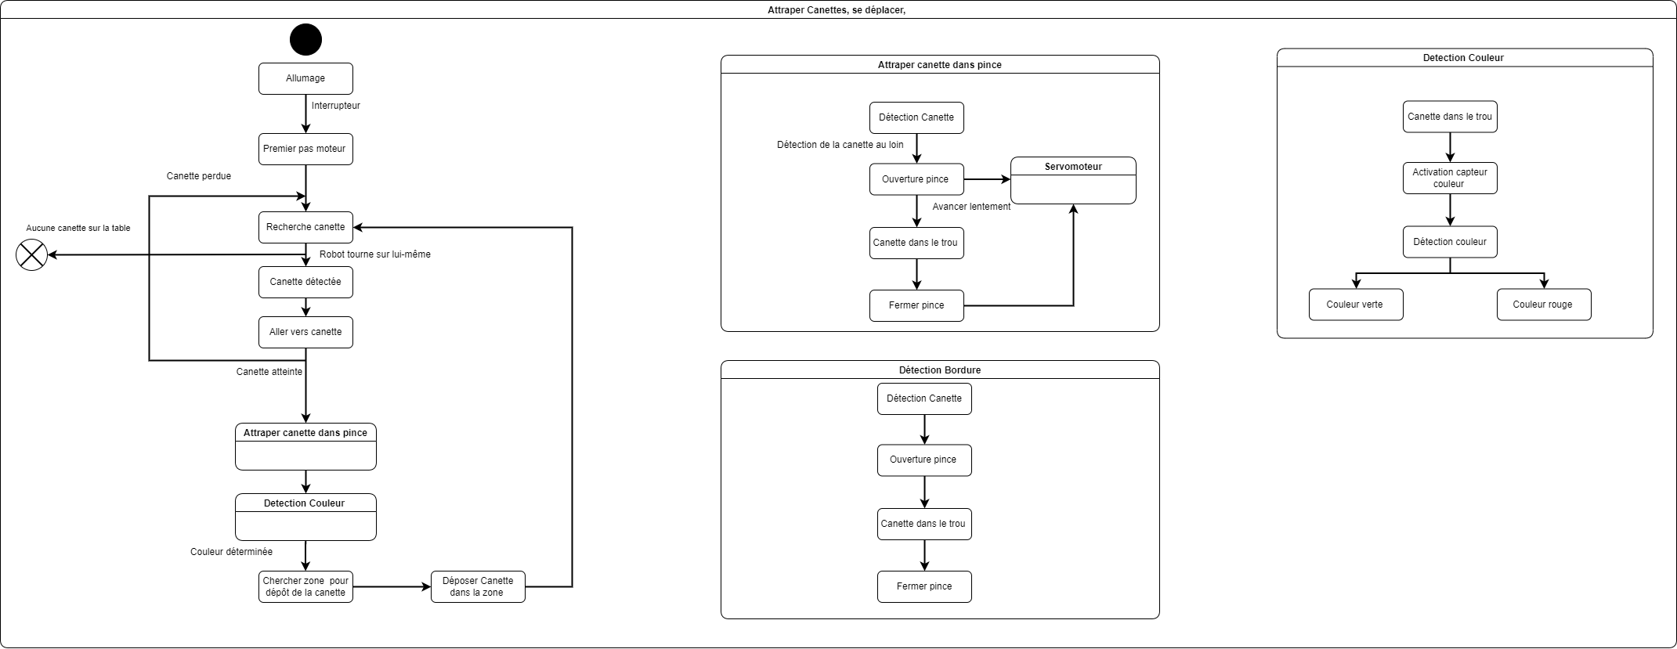
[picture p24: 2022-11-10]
Additional_documents/diagramme_d_etats.png

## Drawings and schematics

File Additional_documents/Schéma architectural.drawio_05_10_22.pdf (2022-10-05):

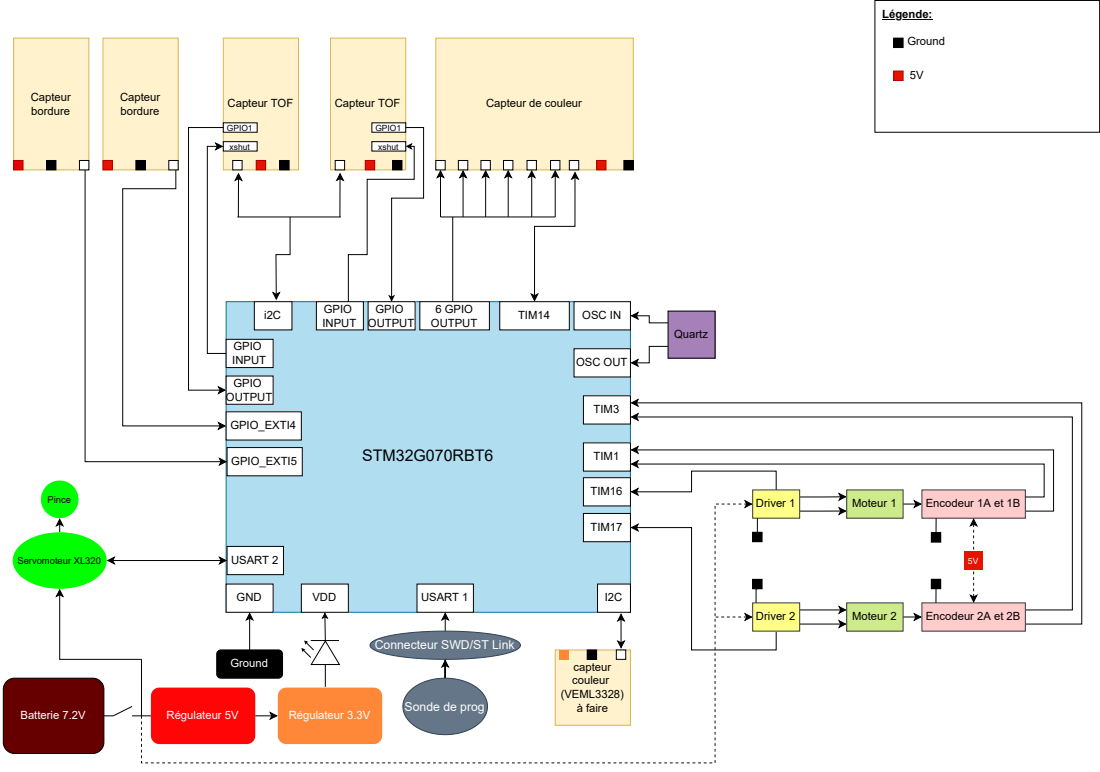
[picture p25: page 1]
Capteur TOF; Capteur de couleur Capteur; bordure; STM32G070RBT6; TIM1; GND; OSC IN; OSC OUT; USART 1; USART 2; TIM3; VDD; Quartz; Capteur bordure; GPIO_EXTI5; GPIO_EXTI4; Batterie 7.2V; Driver 1; Régulateur 5V; Driver 2; Régulateur 3.3V; Moteur 1; Moteur 2; Ground; 6 GPIO; OUTPUT; TIM14; Encodeur 1A et 1B; Légende:; Encodeur 2A et 2B; Servomoteur XL320; Pince; TIM16; TIM17; xshut; GPIO INPUT; GPIO1; GPIO OUTPUT; capteur couleur (VEML3328) à faire

Connecteur SWD/ST Link

Sonde de prog

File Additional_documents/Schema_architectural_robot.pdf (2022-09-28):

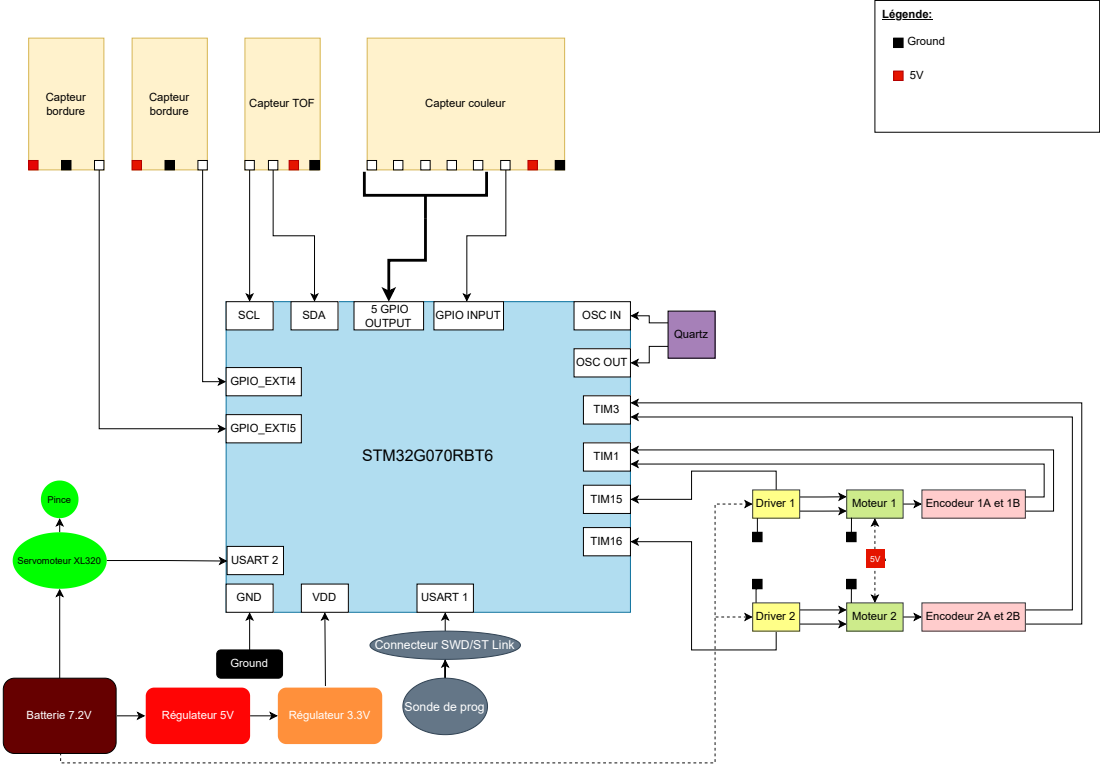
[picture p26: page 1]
Capteur TOF; Capteur couleur Capteur; bordure; STM32G070RBT6; SCL; SDA; TIM1; GND; OSC IN; OSC OUT; USART 1; USART 2; TIM3; VDD; Quartz; Capteur bordure; GPIO_EXTI5; GPIO_EXTI4; Batterie 7.2V; Driver 1; Régulateur 5V; Driver 2; Régulateur 3.3V; Moteur 1; Moteur 2; Ground; 5 GPIO; OUTPUT; GPIO INPUT; Encodeur 1A et 1B; Légende:; Encodeur 2A et 2B; Servomoteur XL320; Pince; TIM15; TIM16

Connecteur SWD/ST Link

Sonde de prog

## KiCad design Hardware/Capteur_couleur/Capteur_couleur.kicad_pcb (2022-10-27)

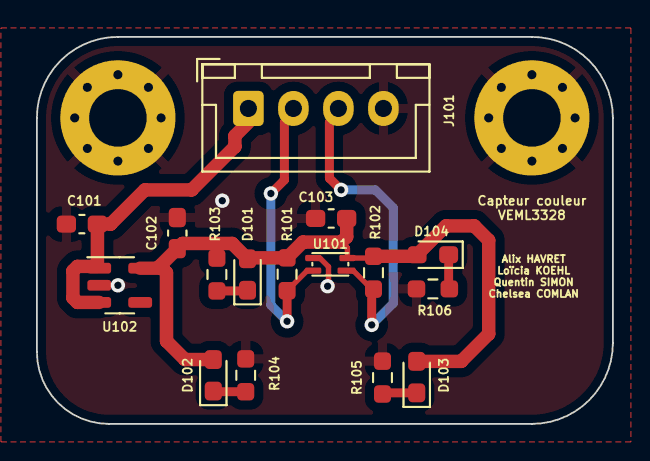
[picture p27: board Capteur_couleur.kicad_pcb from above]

Board: 2 copper layers, 32.0 x 21.5 mm, 18 parts (0 on the bottom side), 9 nets.

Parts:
C101, C102: 1uF; C_0603_1608Metric_Pad1.08x0.95mm_HandSolder
C103: 100n; C_0603_1608Metric_Pad1.08x0.95mm_HandSolder
D101, D102, D103, D104: LED; LED_0603_1608Metric_Pad1.05x0.95mm_HandSolder
H101, H102: MountingHole_Pad; MountingHole_3.2mm_M3_Pad_Via
J101: JST_Couleur_3V; JST_XH_B4B-XH-A_1x04_P2.50mm_Vertical
R101, R102: 2.2k; R_0603_1608Metric_Pad0.98x0.95mm_HandSolder
R103, R104, R105, R106: WHITE; R_0603_1608Metric_Pad0.98x0.95mm_HandSolder
U101: VEML3328
U102: MCP1802x-xx02xOT; SOT-23-5

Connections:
+3.3V: C102.1, C103.1, D101.2 (A), D102.2 (A), D103.2 (A), D104.2 (A), R101.1, R102.1, R103.2, U101.4 (VDD), U102.5 (VOUT)
+5V: C101.1, J101.1, U102.1 (VIN), U102.3 (~SHDN)
GND: C101.2, C102.2, C103.2, H101.1, H102.1, J101.4, R104.2, R105.2, R106.2, U101.1 (GND), U102.2 (GND)
unnamed: D101.1 (K), R103.1
unnamed: D102.1 (K), R104.1
unnamed: D103.1 (K), R105.1
unnamed: D104.1 (K), R106.1
SCL: J101.3, R102.2, U101.3 (SCL)
SDA: J101.2, R101.2, U101.2 (SDA)

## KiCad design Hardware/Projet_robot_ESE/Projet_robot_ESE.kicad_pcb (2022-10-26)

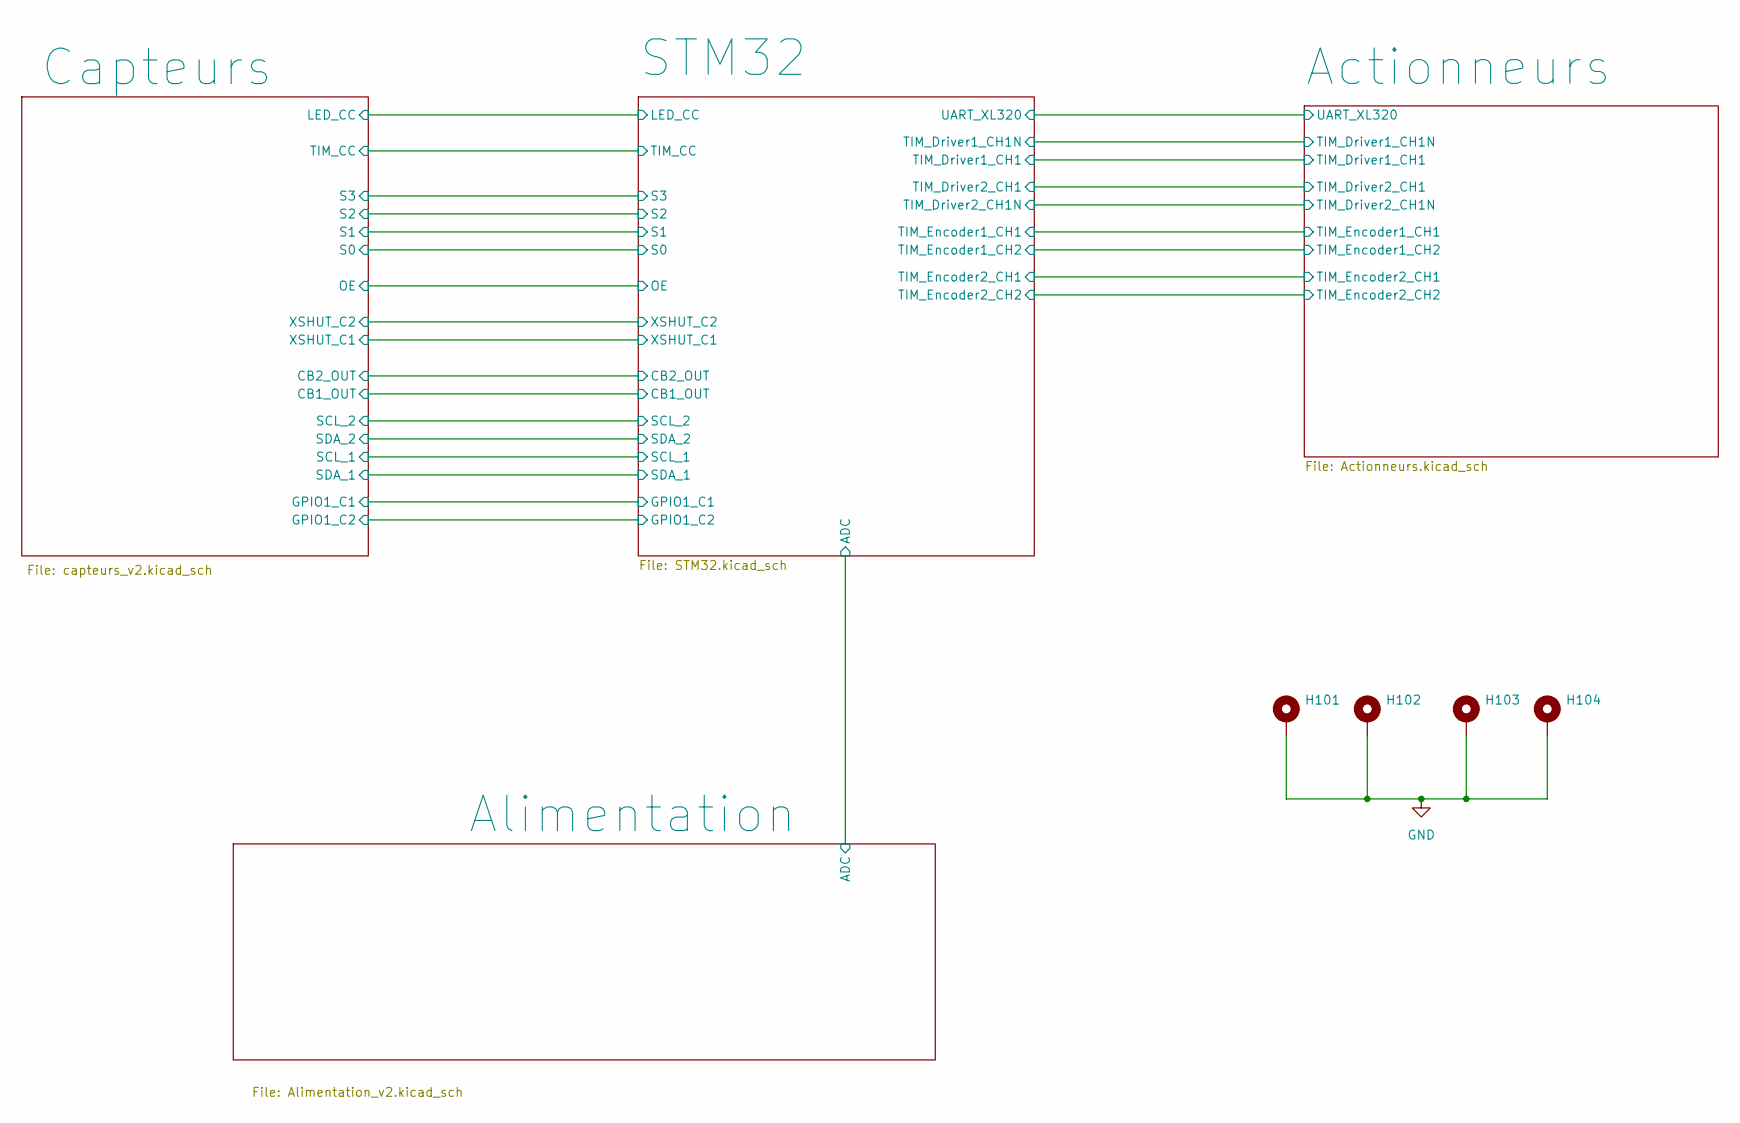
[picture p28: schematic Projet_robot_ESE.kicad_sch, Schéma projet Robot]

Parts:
H101, H102, H103, H104: MountingHole_Pad; MountingHole_3.2mm_M3_Pad_Via

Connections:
GND: H101.1, H102.1, H103.1, H104.1; also elsewhere on the board

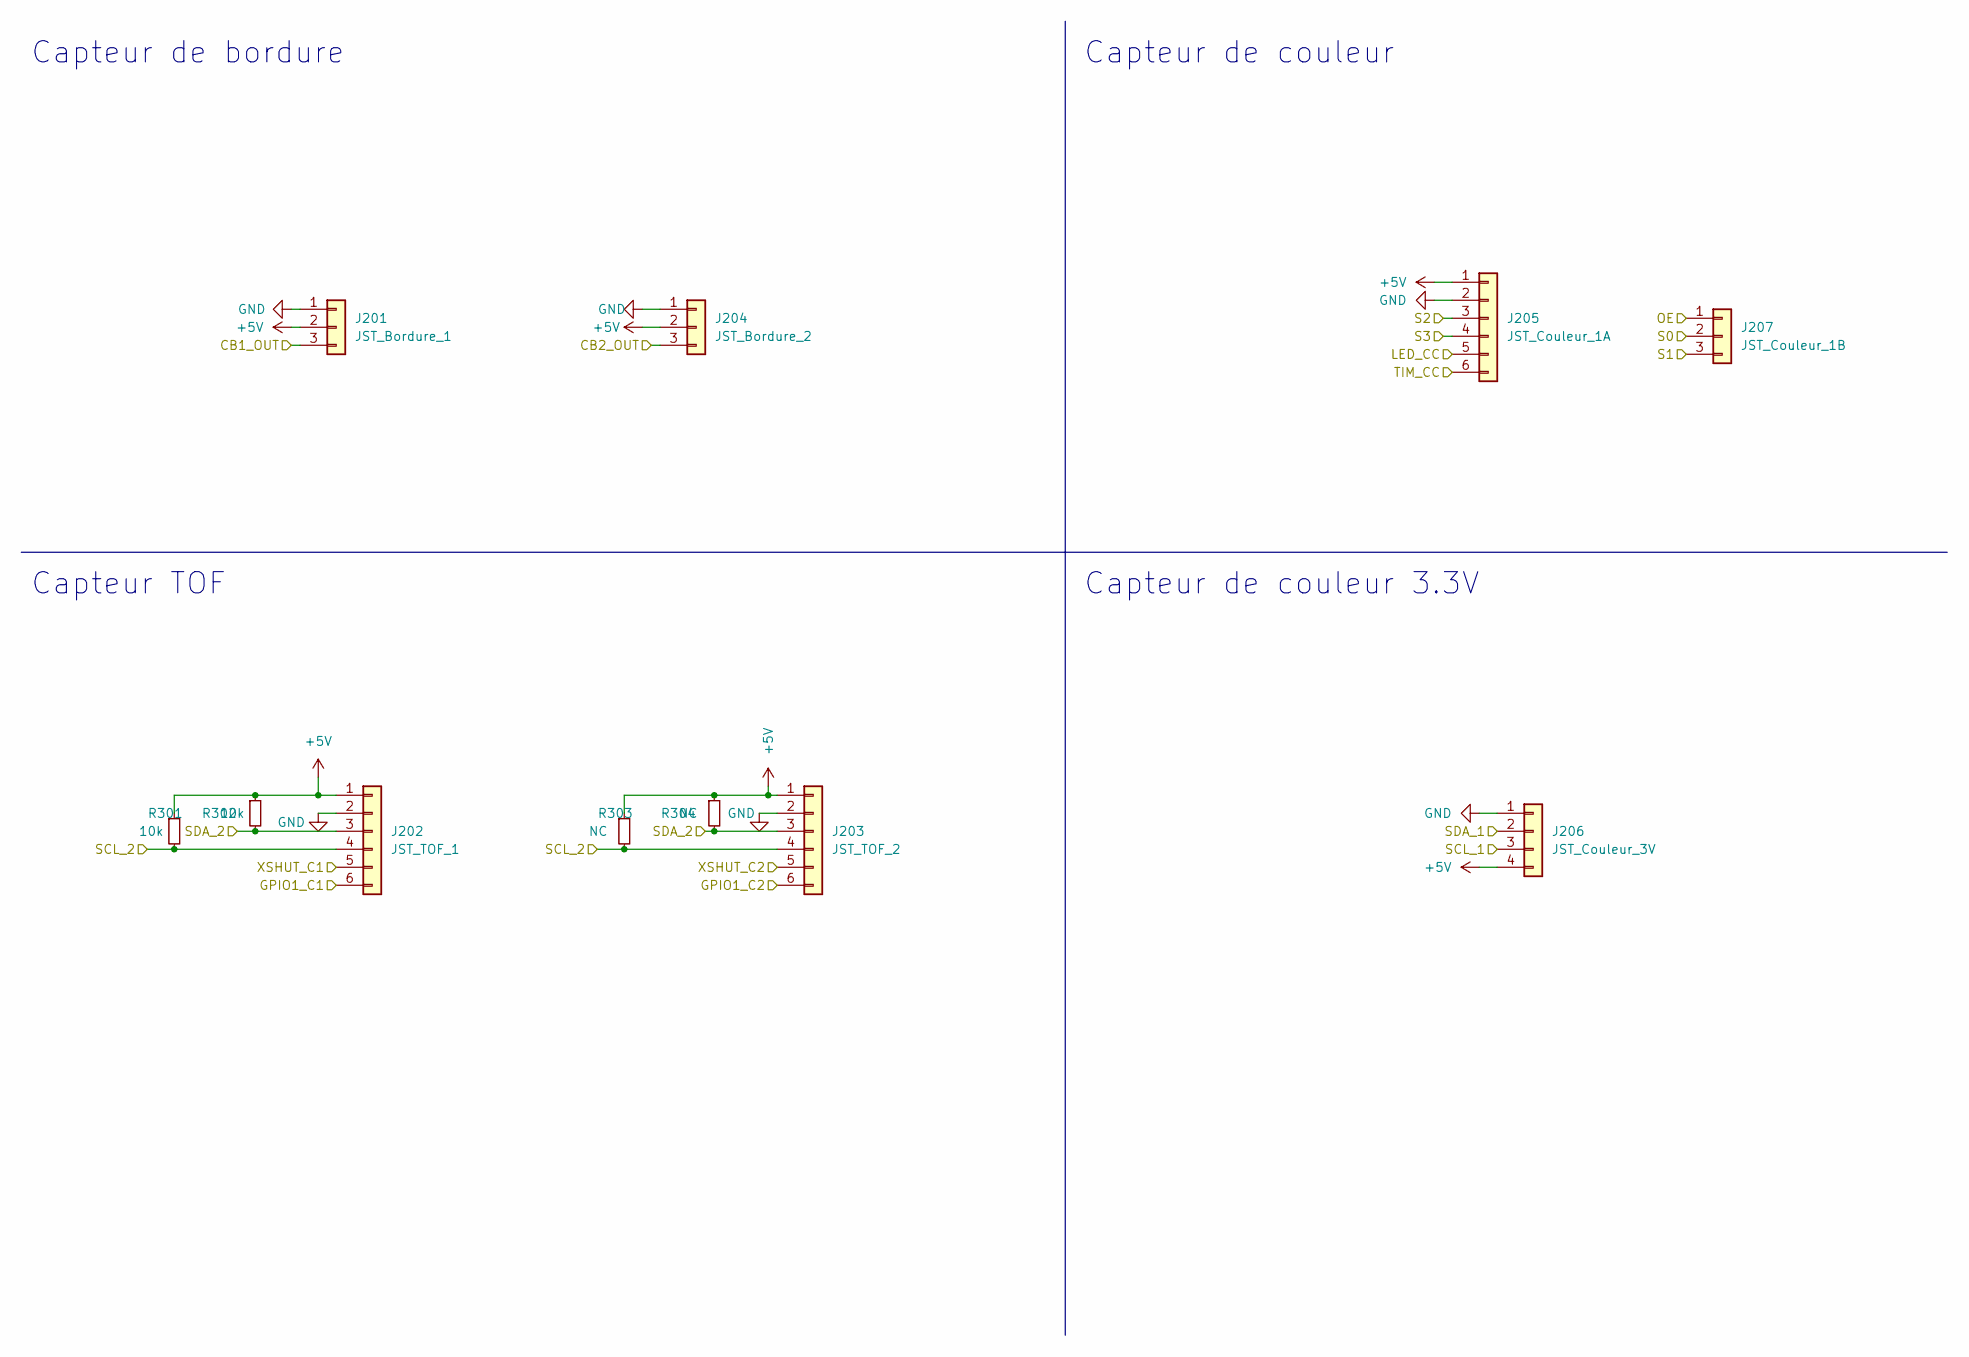
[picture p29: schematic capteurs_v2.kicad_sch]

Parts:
J201: JST_Bordure_1; JST_XH_B3B-XH-A_1x03_P2.50mm_Vertical
J202: JST_TOF_1; JST_XH_B6B-XH-A_1x06_P2.50mm_Vertical
J203: JST_TOF_2; JST_XH_B6B-XH-A_1x06_P2.50mm_Vertical
J204: JST_Bordure_2; JST_XH_B3B-XH-A_1x03_P2.50mm_Vertical
J205: JST_Couleur_1A; JST_XH_B6B-XH-A_1x06_P2.50mm_Vertical
J206: JST_Couleur_3V; JST_XH_B4B-XH-A_1x04_P2.50mm_Vertical
J207: JST_Couleur_1B; JST_XH_B3B-XH-A_1x03_P2.50mm_Vertical
R301, R302: 10k; R_0603_1608Metric_Pad0.98x0.95mm_HandSolder
R303, R304: NC; R_0603_1608Metric_Pad0.98x0.95mm_HandSolder

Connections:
+5V: J201.2, J202.1, J203.1, J204.2, J205.1, J206.4, R301.1, R302.1, R303.1, R304.1; also elsewhere on the board
/Capteurs/CB1_OUT: J201.3; also elsewhere on the board
/Capteurs/CB2_OUT: J204.3; also elsewhere on the board
/Capteurs/GPIO1_C1: J202.6; also elsewhere on the board
/Capteurs/GPIO1_C2: J203.6; also elsewhere on the board
/Capteurs/LED_CC: J205.5; also elsewhere on the board
/Capteurs/OE: J207.1; also elsewhere on the board
/Capteurs/S0: J207.2; also elsewhere on the board
/Capteurs/S1: J207.3; also elsewhere on the board
/Capteurs/S2: J205.3; also elsewhere on the board
/Capteurs/S3: J205.4; also elsewhere on the board
/Capteurs/SCL_1: J206.3; also elsewhere on the board
/Capteurs/SCL_2: J202.4, J203.4, R301.2, R303.2; also elsewhere on the board
/Capteurs/SDA_1: J206.2; also elsewhere on the board
/Capteurs/SDA_2: J202.3, J203.3, R302.2, R304.2; also elsewhere on the board
/Capteurs/TIM_CC: J205.6; also elsewhere on the board
/Capteurs/XSHUT_C1: J202.5; also elsewhere on the board
/Capteurs/XSHUT_C2: J203.5; also elsewhere on the board
GND: J201.1, J202.2, J203.2, J204.1, J205.2, J206.1; also elsewhere on the board

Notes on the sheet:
Capteur de couleur
Capteur TOF
Capteur de couleur 3.3V
Capteur de bordure

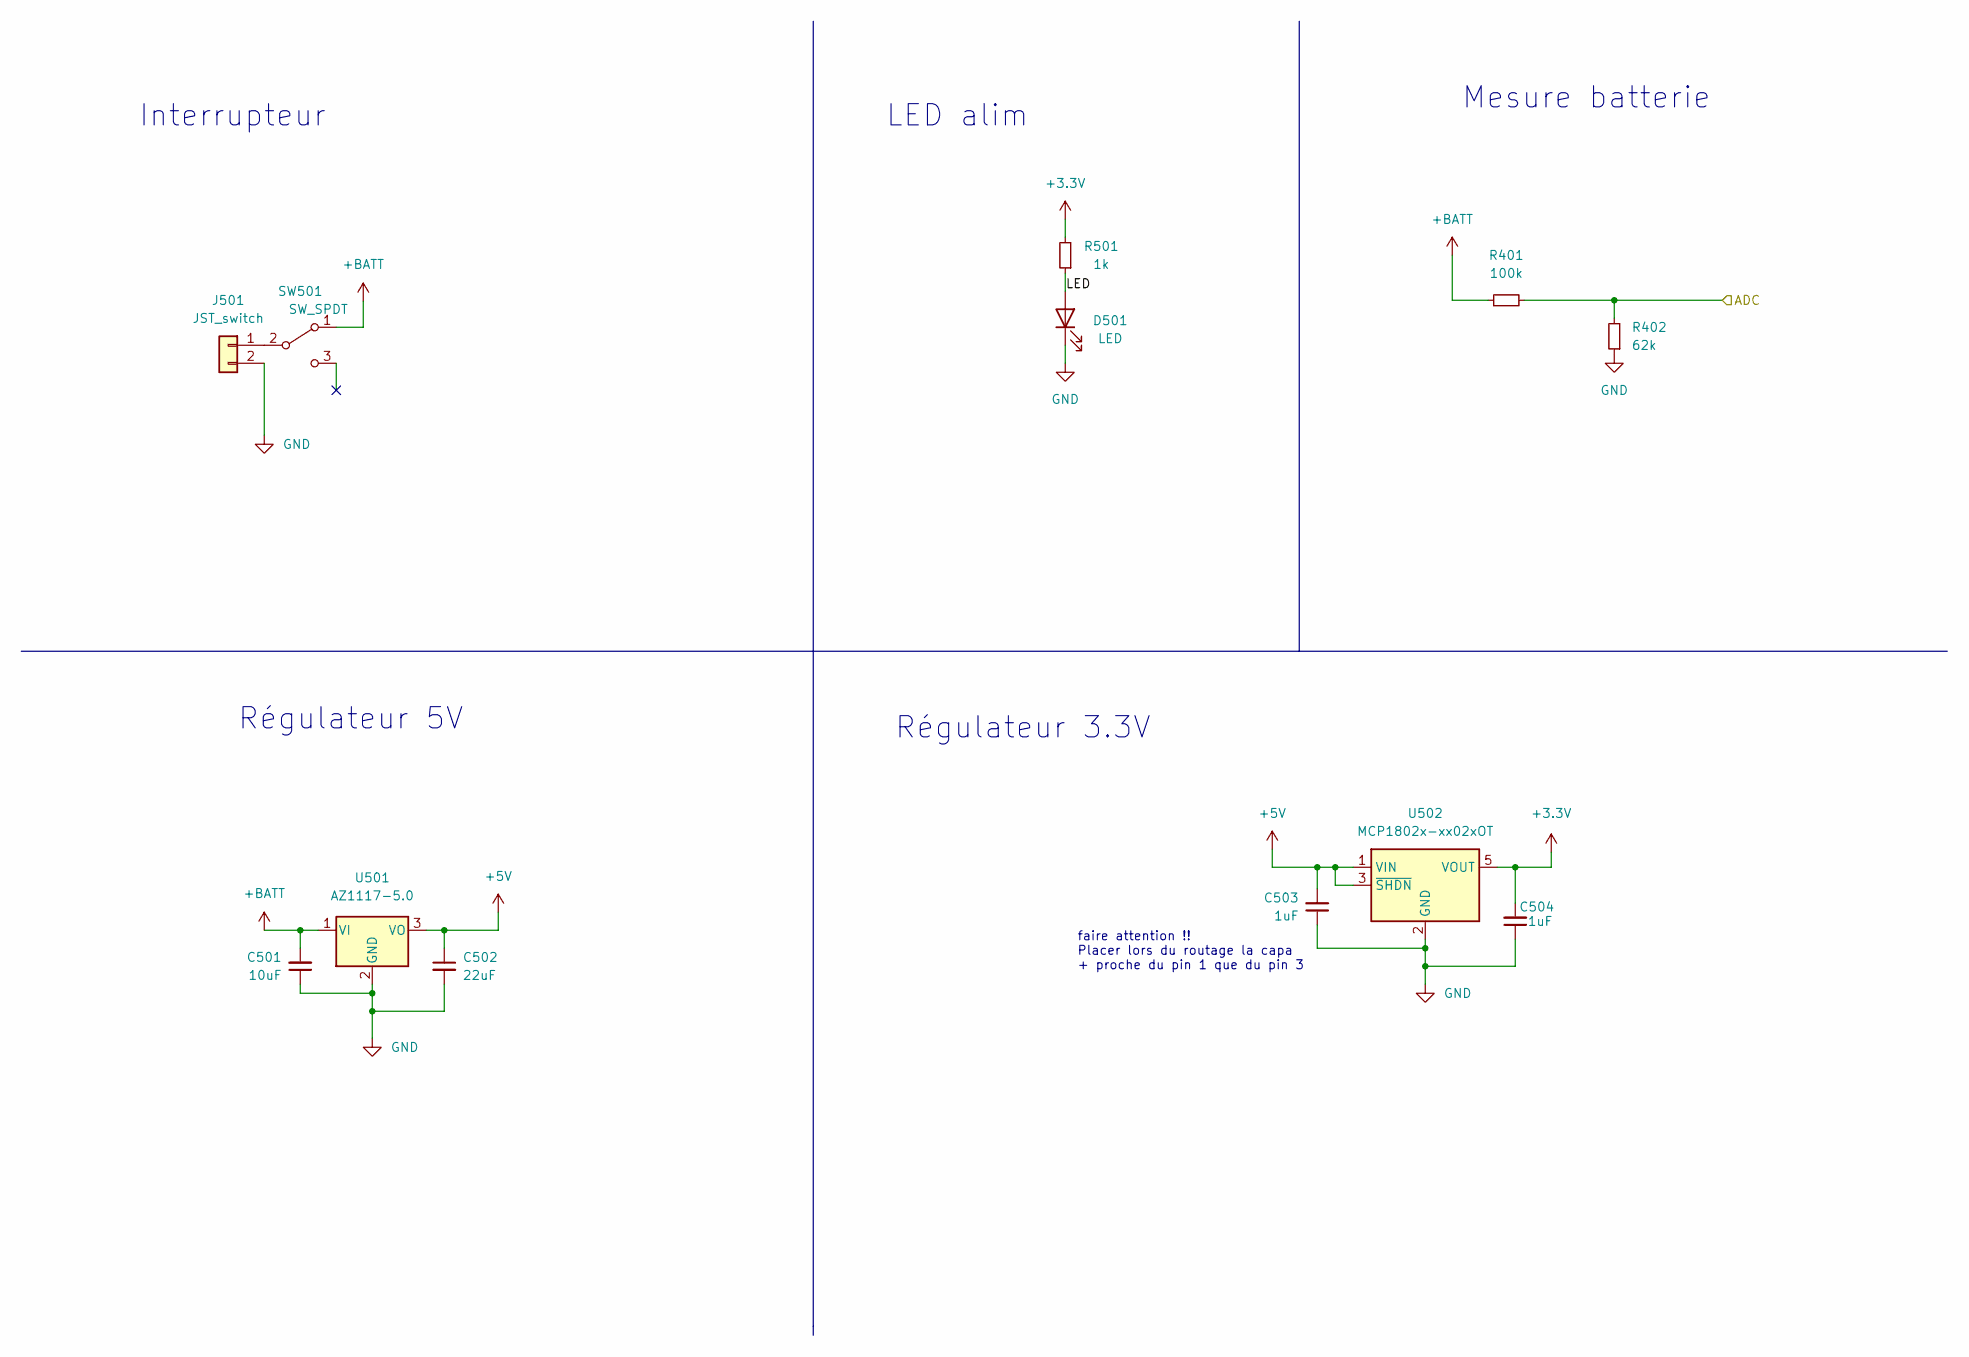
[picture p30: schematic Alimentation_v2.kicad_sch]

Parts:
C501: 10uF; C_0603_1608Metric_Pad1.08x0.95mm_HandSolder
C502: 22uF; C_0603_1608Metric_Pad1.08x0.95mm_HandSolder
C503, C504: 1uF; C_0603_1608Metric_Pad1.08x0.95mm_HandSolder
D501: LED; LED_0603_1608Metric_Pad1.05x0.95mm_HandSolder
J501: JST_switch; JST_XH_B2B-XH-A_1x02_P2.50mm_Vertical
R401: 100k; R_0603_1608Metric_Pad0.98x0.95mm_HandSolder
R402: 62k; R_0603_1608Metric_Pad0.98x0.95mm_HandSolder
R501: 1k; R_0603_1608Metric_Pad0.98x0.95mm_HandSolder
SW501: SW_SPDT; switch_pcb_robot
U501: AZ1117-5.0; SOT-223-3_TabPin2
U502: MCP1802x-xx02xOT; SOT-23-5

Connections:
+3.3V: C504.2, R501.2, U502.5 (VOUT); also elsewhere on the board
+5V: C502.1, C503.2, U501.3 (VO), U502.1 (VIN), U502.3 (~SHDN); also elsewhere on the board
+BATT: C501.2, R401.1, SW501.1 (A), U501.1 (VI); also elsewhere on the board
/Alimentation/ADC: R401.2, R402.2; also elsewhere on the board
/Alimentation/LED: D501.2 (A), R501.1
GND: C501.1, C502.2, C503.1, C504.1, D501.1 (K), J501.2, R402.1, U501.2 (GND), U502.2 (GND); also elsewhere on the board
unnamed: J501.1, SW501.2 (B)

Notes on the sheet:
Interrupteur
Régulateur 5V
LED alim
faire attention !! Placer lors du routage la capa + proche du pin 1 que du pin 3
Mesure batterie
Régulateur 3.3V

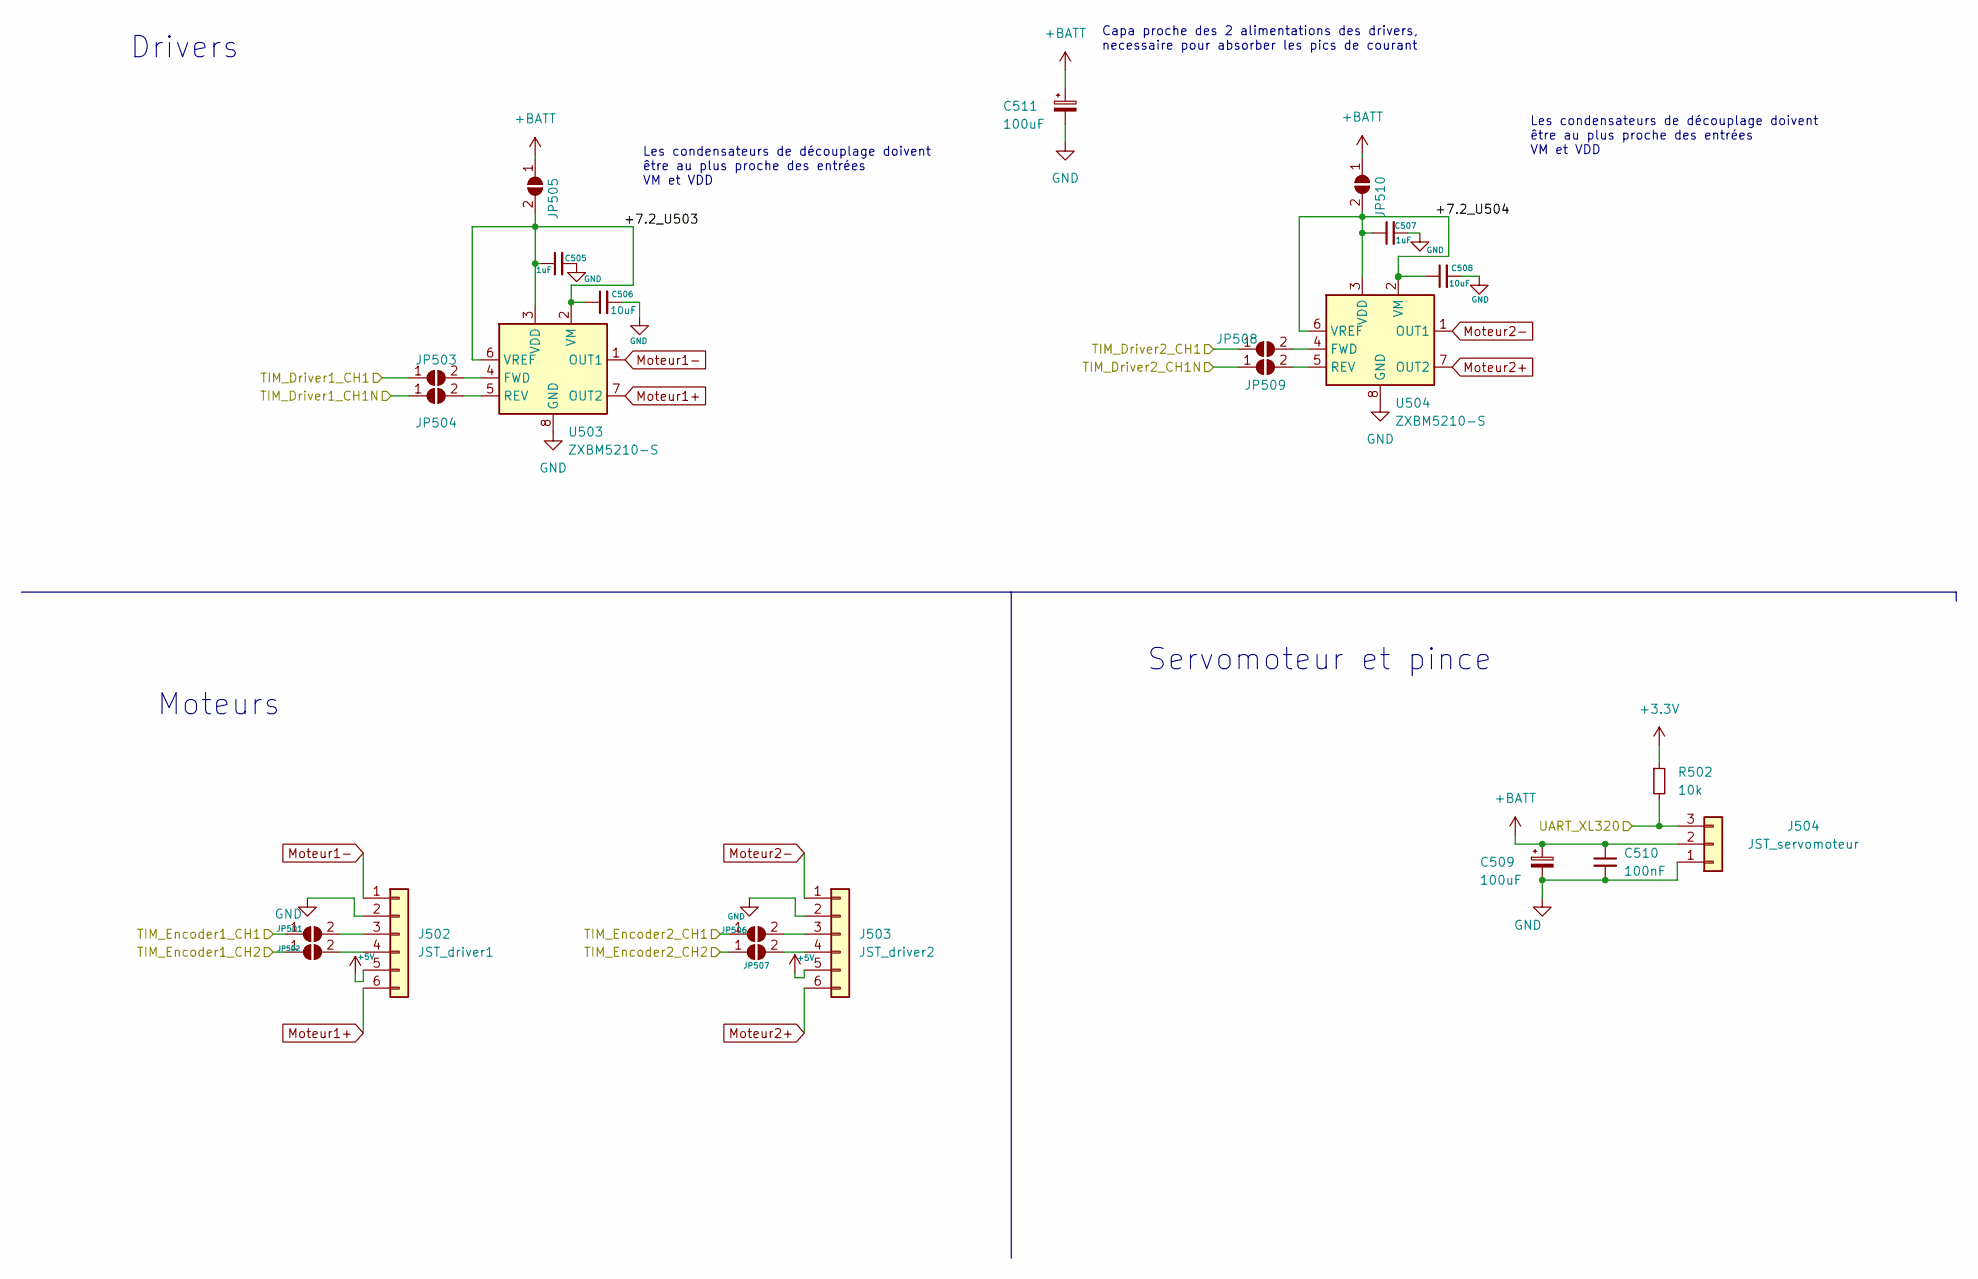
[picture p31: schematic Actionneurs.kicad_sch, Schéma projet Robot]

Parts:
C505, C507: 1uF; C_0603_1608Metric_Pad1.08x0.95mm_HandSolder
C506, C508: 10uF; C_0603_1608Metric_Pad1.08x0.95mm_HandSolder
C509, C511: 100uF; CP_Radial_D6.3mm_P2.50mm
C510: 100nF; C_0603_1608Metric_Pad1.08x0.95mm_HandSolder
J502: JST_driver1; JST_XH_B6B-XH-A_1x06_P2.50mm_Vertical
J503: JST_driver2; JST_XH_B6B-XH-A_1x06_P2.50mm_Vertical
J504: JST_servomoteur; JST_XH_B3B-XH-A_1x03_P2.50mm_Vertical
JP501, JP502, JP503, JP504, JP505, JP506, JP507, JP508, JP509, JP510: SolderJumper_2_Open; SolderJumper-2_P1.3mm_Open_TrianglePad1.0x1.5mm
R502: 10k; R_0603_1608Metric_Pad0.98x0.95mm_HandSolder
U503, U504: ZXBM5210-S; SOIC-8_3.9x4.9mm_P1.27mm

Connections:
+3.3V: R502.1; also elsewhere on the board
+5V: J502.5, J503.5; also elsewhere on the board
+BATT: C509.1, C510.1, C511.1, J504.2, JP505.1 (A), JP510.1 (A); also elsewhere on the board
/Actionneurs/+7.2_U503: C505.1, C506.1, JP505.2 (B), U503.2 (VM), U503.3 (VDD), U503.6 (VREF)
/Actionneurs/+7.2_U504: C507.1, C508.1, JP510.2 (B), U504.2 (VM), U504.3 (VDD), U504.6 (VREF)
/Actionneurs/TIM_Driver1_CH1: JP503.1 (A); also elsewhere on the board
/Actionneurs/TIM_Driver1_CH1N: JP504.1 (A); also elsewhere on the board
/Actionneurs/TIM_Driver2_CH1: JP508.1 (A); also elsewhere on the board
/Actionneurs/TIM_Driver2_CH1N: JP509.1 (A); also elsewhere on the board
/Actionneurs/TIM_Encoder1_CH1: JP501.1 (A); also elsewhere on the board
/Actionneurs/TIM_Encoder1_CH2: JP502.1 (A); also elsewhere on the board
/Actionneurs/TIM_Encoder2_CH1: JP506.1 (A); also elsewhere on the board
/Actionneurs/TIM_Encoder2_CH2: JP507.1 (A); also elsewhere on the board
/Actionneurs/UART_XL320: J504.3, R502.2; also elsewhere on the board
GND: C505.2, C506.2, C507.2, C508.2, C509.2, C510.2, C511.2, J502.2, J503.2, J504.1, U503.8 (GND), U504.8 (GND); also elsewhere on the board
Moteur1+: J502.6, U503.7 (OUT2)
Moteur1-: J502.1, U503.1 (OUT1)
Moteur2+: J503.6, U504.7 (OUT2)
Moteur2-: J503.1, U504.1 (OUT1)
unnamed: J502.3, JP501.2 (B)
unnamed: J502.4, JP502.2 (B)
unnamed: J503.3, JP506.2 (B)
unnamed: J503.4, JP507.2 (B)
unnamed: JP503.2 (B), U503.4 (FWD)
unnamed: JP504.2 (B), U503.5 (REV)
unnamed: JP508.2 (B), U504.4 (FWD)
unnamed: JP509.2 (B), U504.5 (REV)

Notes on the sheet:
Les condensateurs de découplage doivent être au plus proche des entrées VM et VDD
Servomoteur et pince
Drivers
Moteurs
Capa proche des 2 alimentations des drivers, necessaire pour absorber les pics de courant

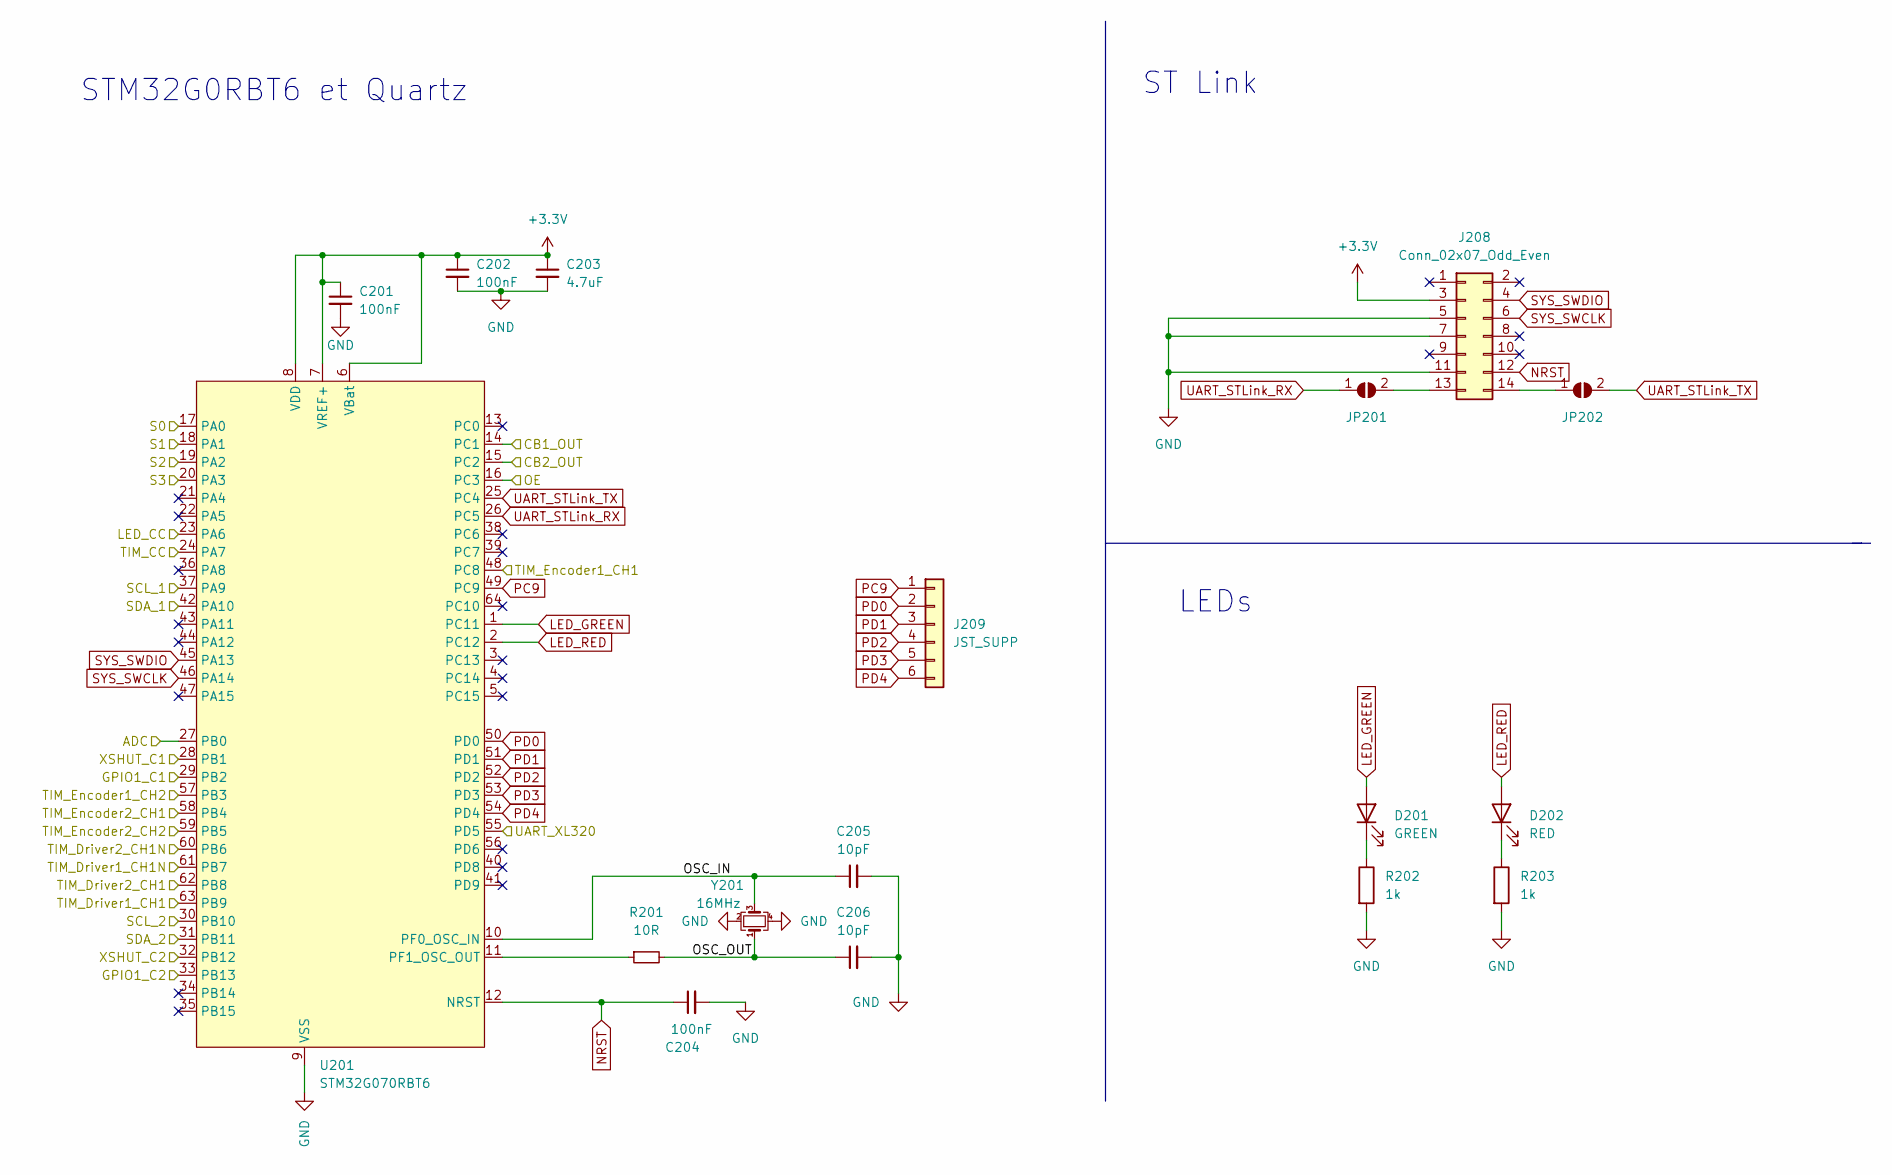
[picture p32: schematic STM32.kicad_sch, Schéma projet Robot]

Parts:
C201, C202, C204: 100nF; C_0603_1608Metric_Pad1.08x0.95mm_HandSolder
C203: 4.7uF; C_0603_1608Metric_Pad1.08x0.95mm_HandSolder
C205, C206: 10pF; C_0603_1608Metric_Pad1.08x0.95mm_HandSolder
D201: GREEN; LED_0603_1608Metric_Pad1.05x0.95mm_HandSolder
D202: RED; LED_0603_1608Metric_Pad1.05x0.95mm_HandSolder
J208: Conn_02x07_Odd_Even; PinHeader_2x07_P1.27mm_Vertical_SMD
J209: JST_SUPP; PinHeader_1x06_P2.54mm_Vertical
JP201, JP202: SolderJumper_2_Open; SolderJumper-2_P1.3mm_Open_TrianglePad1.0x1.5mm
R201: 10R; R_0603_1608Metric_Pad0.98x0.95mm_HandSolder
R202, R203: 1k; R_0603_1608Metric_Pad0.98x0.95mm_HandSolder
U201: STM32G070RBT6; LQFP-64_10x10mm_P0.5mm
Y201: 16MHz; Crystal_SMD_EuroQuartz_MT-4Pin_3.2x2.5mm

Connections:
+3.3V: C201.1, C202.1, C203.1, J208.3, U201.6 (VBat), U201.7 (VREF+), U201.8 (VDD); also elsewhere on the board
/Actionneurs/TIM_Driver1_CH1: U201.63 (PB9); also elsewhere on the board
/Actionneurs/TIM_Driver1_CH1N: U201.61 (PB7); also elsewhere on the board
/Actionneurs/TIM_Driver2_CH1: U201.62 (PB8); also elsewhere on the board
/Actionneurs/TIM_Driver2_CH1N: U201.60 (PB6); also elsewhere on the board
/Actionneurs/TIM_Encoder1_CH1: U201.48 (PC8); also elsewhere on the board
/Actionneurs/TIM_Encoder1_CH2: U201.57 (PB3); also elsewhere on the board
/Actionneurs/TIM_Encoder2_CH1: U201.58 (PB4); also elsewhere on the board
/Actionneurs/TIM_Encoder2_CH2: U201.59 (PB5); also elsewhere on the board
/Actionneurs/UART_XL320: U201.55 (PD5); also elsewhere on the board
/Alimentation/ADC: U201.27 (PB0); also elsewhere on the board
/Capteurs/CB1_OUT: U201.14 (PC1); also elsewhere on the board
/Capteurs/CB2_OUT: U201.15 (PC2); also elsewhere on the board
/Capteurs/GPIO1_C1: U201.29 (PB2); also elsewhere on the board
/Capteurs/GPIO1_C2: U201.33 (PB13); also elsewhere on the board
/Capteurs/LED_CC: U201.23 (PA6); also elsewhere on the board
/Capteurs/OE: U201.16 (PC3); also elsewhere on the board
/Capteurs/S0: U201.17 (PA0); also elsewhere on the board
/Capteurs/S1: U201.18 (PA1); also elsewhere on the board
/Capteurs/S2: U201.19 (PA2); also elsewhere on the board
/Capteurs/S3: U201.20 (PA3); also elsewhere on the board
/Capteurs/SCL_1: U201.37 (PA9); also elsewhere on the board
/Capteurs/SCL_2: U201.30 (PB10); also elsewhere on the board
/Capteurs/SDA_1: U201.42 (PA10); also elsewhere on the board
/Capteurs/SDA_2: U201.31 (PB11); also elsewhere on the board
/Capteurs/TIM_CC: U201.24 (PA7); also elsewhere on the board
/Capteurs/XSHUT_C1: U201.28 (PB1); also elsewhere on the board
/Capteurs/XSHUT_C2: U201.32 (PB12); also elsewhere on the board
/STM32/OSC_IN: C205.1, U201.10 (PF0_OSC_IN), Y201.3
/STM32/OSC_OUT: C206.1, R201.2, Y201.1
GND: C201.2, C202.2, C203.2, C204.2, C205.2, C206.2, J208.5, J208.7, J208.11, R202.2, R203.2, U201.9 (VSS), Y201.2, Y201.4; also elsewhere on the board
LED_GREEN: D201.2 (A), U201.1 (PC11)
LED_RED: D202.2 (A), U201.2 (PC12)
NRST: C204.1, J208.12, U201.12 (NRST)
unnamed: D201.1 (K), R202.1
unnamed: D202.1 (K), R203.1
unnamed: J208.13, JP201.2 (B)
unnamed: J208.14, JP202.1 (A)
unnamed: R201.1, U201.11 (PF1_OSC_OUT)
PC9: J209.1, U201.49 (PC9)
PD0: J209.2, U201.50 (PD0)
PD1: J209.3, U201.51 (PD1)
PD2: J209.4, U201.52 (PD2)
PD3: J209.5, U201.53 (PD3)
PD4: J209.6, U201.54 (PD4)
SYS_SWCLK: J208.6, U201.46 (PA14)
SYS_SWDIO: J208.4, U201.45 (PA13)
UART_STLink_RX: JP201.1 (A), U201.26 (PC5)
UART_STLink_TX: JP202.2 (B), U201.25 (PC4)

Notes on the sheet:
STM32G0RBT6 et Quartz
LEDs
ST Link

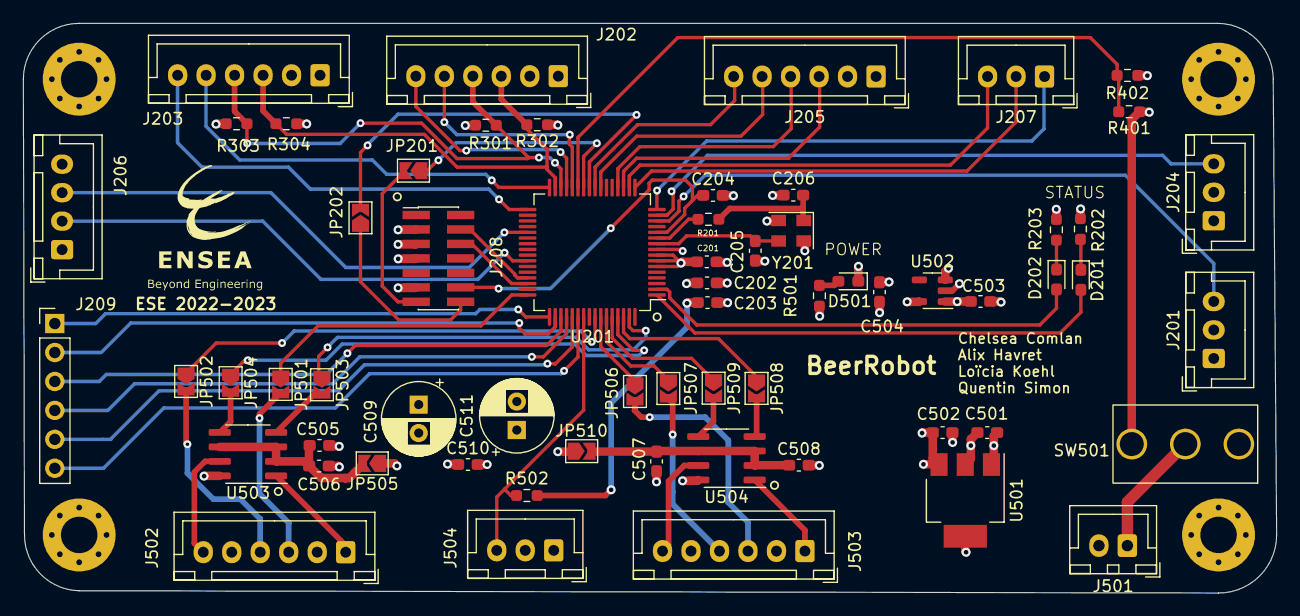
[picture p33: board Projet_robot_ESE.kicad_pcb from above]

Board: 4 copper layers, 110.0 x 50.0 mm, 67 parts (0 on the bottom side), 67 nets.

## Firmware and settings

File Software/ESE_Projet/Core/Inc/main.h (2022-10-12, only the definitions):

#define CB1_OUT_Pin GPIO_PIN_1
#define CB1_OUT_GPIO_Port GPIOC
#define CB2_OUT_Pin GPIO_PIN_2
#define CB2_OUT_GPIO_Port GPIOC
#define S0_Pin GPIO_PIN_0
#define S0_GPIO_Port GPIOA
#define S1_Pin GPIO_PIN_1
#define S1_GPIO_Port GPIOA
#define S2_Pin GPIO_PIN_2
#define S2_GPIO_Port GPIOA
#define S3_Pin GPIO_PIN_3
#define S3_GPIO_Port GPIOA
#define TIM_CC_Pin GPIO_PIN_4
#define TIM_CC_GPIO_Port GPIOA
#define OE_Pin GPIO_PIN_5
#define OE_GPIO_Port GPIOA
#define LED_CC_Pin GPIO_PIN_6
#define LED_CC_GPIO_Port GPIOA
#define UART_STLink_TX_Pin GPIO_PIN_4
#define UART_STLink_TX_GPIO_Port GPIOC
#define UART_STLink_RX_Pin GPIO_PIN_5
#define UART_STLink_RX_GPIO_Port GPIOC
#define XSHUT_C1_Pin GPIO_PIN_1
#define XSHUT_C1_GPIO_Port GPIOB
#define GPIO1_C1_Pin GPIO_PIN_2
#define GPIO1_C1_GPIO_Port GPIOB
#define SCL_2_Pin GPIO_PIN_10
#define SCL_2_GPIO_Port GPIOB
#define SDA_2_Pin GPIO_PIN_11
#define SDA_2_GPIO_Port GPIOB
#define XSHUT_C2_Pin GPIO_PIN_12
#define XSHUT_C2_GPIO_Port GPIOB
#define GPIO1_C2_Pin GPIO_PIN_13
#define GPIO1_C2_GPIO_Port GPIOB
#define SCL_1_Pin GPIO_PIN_9
#define SCL_1_GPIO_Port GPIOA
#define SDA_1_Pin GPIO_PIN_10
#define SDA_1_GPIO_Port GPIOA
#define TIM_Encoder1_CH1_Pin GPIO_PIN_8
#define TIM_Encoder1_CH1_GPIO_Port GPIOC
#define UART_XL320_Pin GPIO_PIN_5
#define UART_XL320_GPIO_Port GPIOD
#define TIM_Encoder1_CH2_Pin GPIO_PIN_3
#define TIM_Encoder1_CH2_GPIO_Port GPIOB
#define TIM_Encoder2_CH1_Pin GPIO_PIN_4
#define TIM_Encoder2_CH1_GPIO_Port GPIOB
#define TIM_Encoder2_CH2_Pin GPIO_PIN_5
#define TIM_Encoder2_CH2_GPIO_Port GPIOB
#define TIM_Driver2_CH1N_Pin GPIO_PIN_6
#define TIM_Driver2_CH1N_GPIO_Port GPIOB
#define TIM_Driver1_CH1N_Pin GPIO_PIN_7
#define TIM_Driver1_CH1N_GPIO_Port GPIOB
#define TIM_Driver2_CH1_Pin GPIO_PIN_8
#define TIM_Driver2_CH1_GPIO_Port GPIOB
#define TIM_Driver1_CH1_Pin GPIO_PIN_9
#define TIM_Driver1_CH1_GPIO_Port GPIOB

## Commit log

2022-10-10 Add KiCad_Schematic
    [Alimentation.kicad_sch, Moteurs.kicad_sch, Projet_robot_ESE.kicad_pcb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]
2022-10-12 V2 schematic
    [Actionneurs.kicad_sch, Alimentation_v2.kicad_sch, Moteurs.kicad_sch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]
2022-10-17 Update placement PCB
    [Actionneurs.kicad_sch, Alimentation_v2.kicad_sch, Moteurs.kicad_sch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]
2022-10-17 Update Schematic v2
    [Actionneurs.kicad_sch, Alimentation_v2.kicad_sch, Moteurs.kicad_sch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]
2022-10-19 Final placement
    [Actionneurs.kicad_sch, Alimentation_v2.kicad_sch, Projet_robot_ESE.kicad_pcb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]
2022-10-19 Error commit
    [Actionneurs.kicad_sch, Alimentation_v2.kicad_sch, Moteurs.kicad_sch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]
2022-10-20 update routage
    [Actionneurs.kicad_sch, Alimentation_v2.kicad_sch, Moteurs.kicad_sch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]
2022-10-24 Capteur couleur 3.3V
    [Capteur_couleur.kicad_pcb, Capteur_couleur.kicad_sch]
2022-10-26 Update servomoteur
    [Actionneurs.kicad_sch, Projet_robot_ESE.kicad_pcb, Projet_robot_ESE.kicad_sch]
2022-10-27 Update Capteur couleur
    [Capteur_couleur.kicad_pcb]
2022-10-27 Update footprint
    [Capteur_couleur.kicad_pcb]
2022-11-13 Rapport de mi-avancement projet

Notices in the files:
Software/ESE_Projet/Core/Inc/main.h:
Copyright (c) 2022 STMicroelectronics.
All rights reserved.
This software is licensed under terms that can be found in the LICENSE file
